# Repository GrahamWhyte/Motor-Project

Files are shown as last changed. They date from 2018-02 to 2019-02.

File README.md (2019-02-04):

# Motor-Project
3rd Year UBC Design project. 

Objective: Design a system of two motors to control a laser to draw various shapes fast enough to look like a complete image. The motors must be hand-built and controlled with a PID controller. 

Files are organized as follows:

1. Elec391_Project_Gen_1 -> Initial PCB
2. Elec391_Project_Gen_2 -> Revised PCB 
3. Elec391_Project_Software -> Arduino Code and GUI 
4. Tests -> Arduino Code to run various tests on Motor. These are flashed onto the Arduino and then run using main.py in Data
5. Data -> Data logger code and output 
6. Matlab and Simulink -> Various models and Matlab scripts
7. Speed Tests -> A series of tests conducted on the custom motors to see how fast they can go! 
8. Encoder -> Mechanical design of test rig 
9. ControlSlideDeck-B10.pdf: Final presentation

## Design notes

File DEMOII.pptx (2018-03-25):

## B10 – “The Rocket Men”

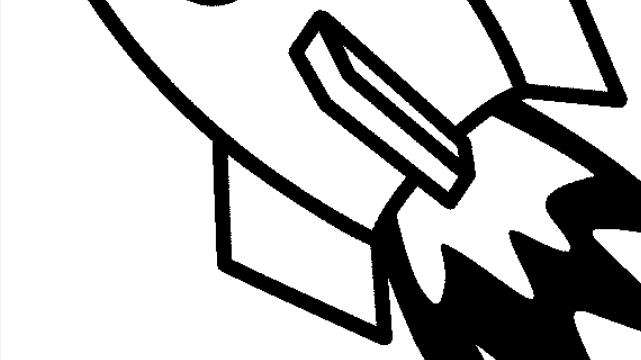
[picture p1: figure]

Control Group
Matthew Gill – 13249157
Graham Whyte - 45688158

## RCGs

Requirement
50 ms Instruction time / Rise Time less than 50 ms
Less than 5% overshoot
2-DOF Spherical Wrist
Simulink Model
Real-Time Controller
Constraints
16 MHz CPU clock speed
Budget ($1000 UBCD + $400 CAD)
Goals
Everything on PCBs
Separate Laser Power – No Dangling Wires from Diode
Animation
Optimal Rise – 25 ms
Satisfied
Satisfied
Satisfied

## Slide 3

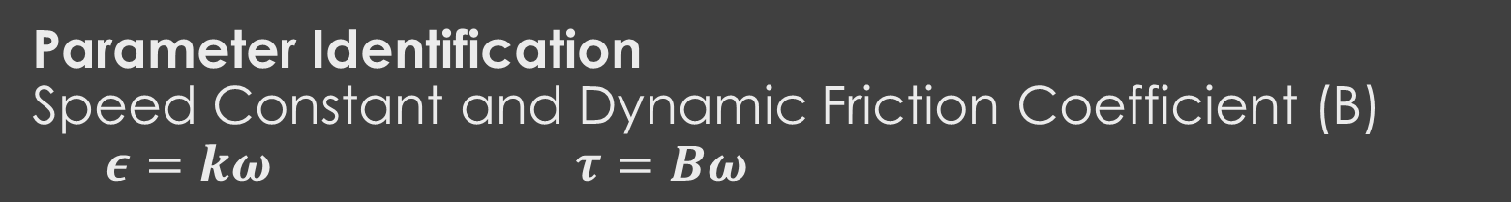
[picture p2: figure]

- Steady State Unloaded Voltage Tests
  - Current Draw (I) and Angular Velocity ( ω ) Recorded
- Back EMF ( ε ) calculated from current & terminal resistance
  - Terminal Resistance & Inductance measured with RLC meter
- Speed Constant (K) as slope of Velocity/Back EMF curve
- Friction Coefficient (B) as Slope of Torque / Speed Curve
  - Torque calculated with: τ=kI

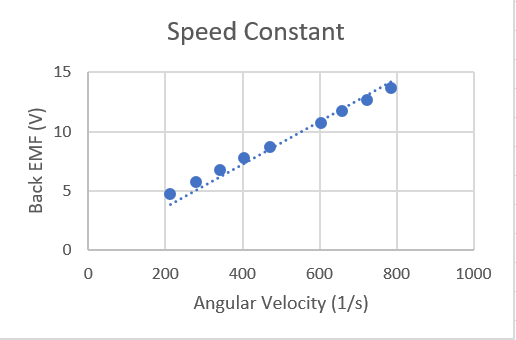
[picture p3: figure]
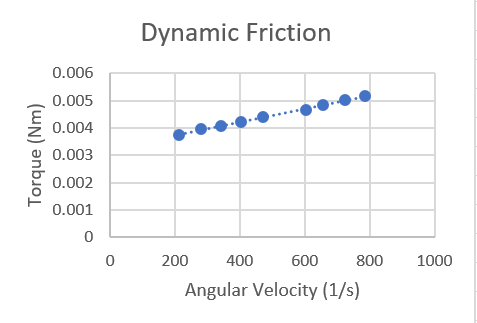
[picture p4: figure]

## Parameter Identification Rotor Inertia (J) - Deceleration test of unloaded motor

J =8.30 gcm^2

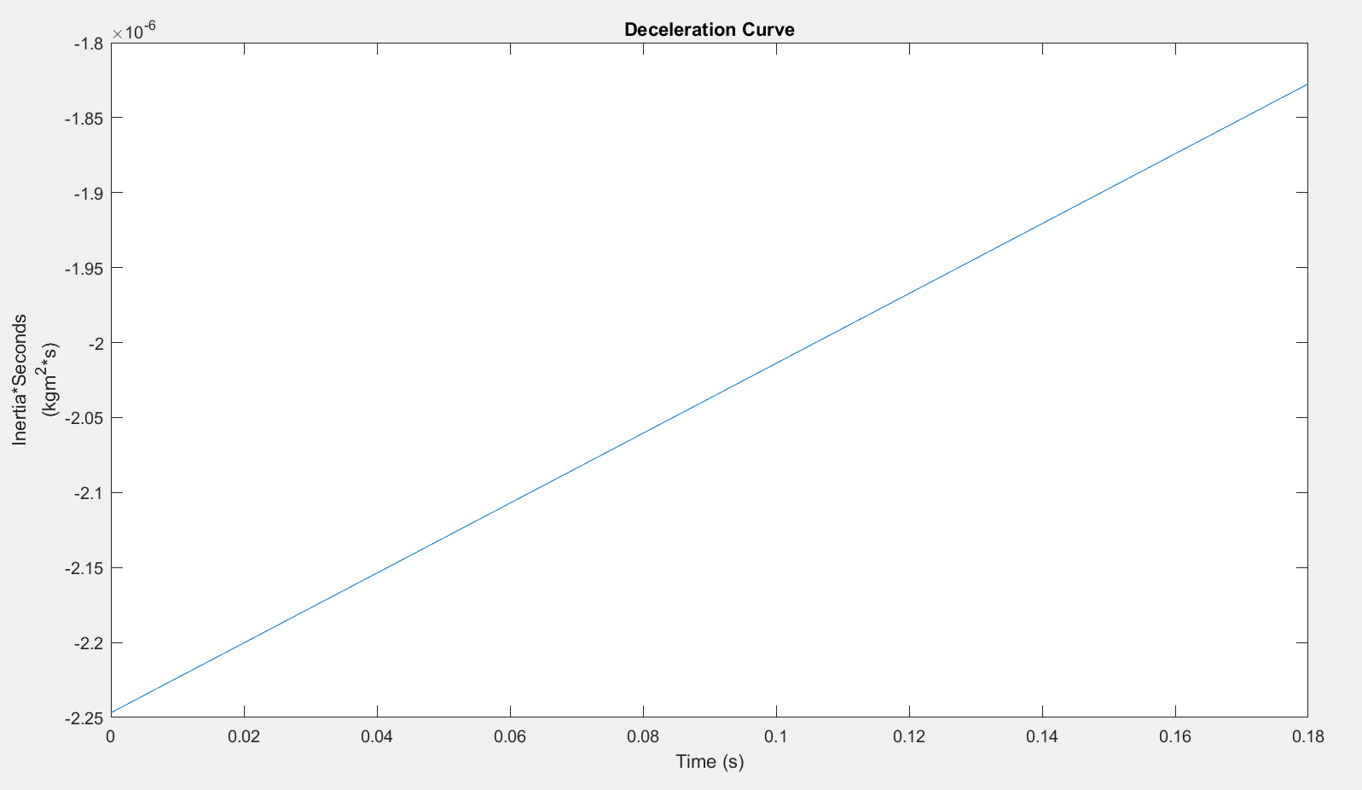
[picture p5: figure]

- Angular System with no external Torque:
0=Jω+Bω
then:
J is Slope of−(B∗ω(t))/(ω(t)) curve
- Power is cut to motor running constant velocity and velocity and acceleration is recorded as motor slows

## Experimental Step Response Curve Fitting

- Step test is conducted by applying a 10V step voltage to motor and recording position of motor
- The Velocity Step Response is obtained by differentiating the Position Step Response
- Utilizing MATLAB's System Identification toolkit a transfer function can then be fitted to the Velocity Response
- Transfer Function from Velocity Step Response
- (ω(s))/(V(s))(2.702x10^4)/(s^2 +38.02s+531)

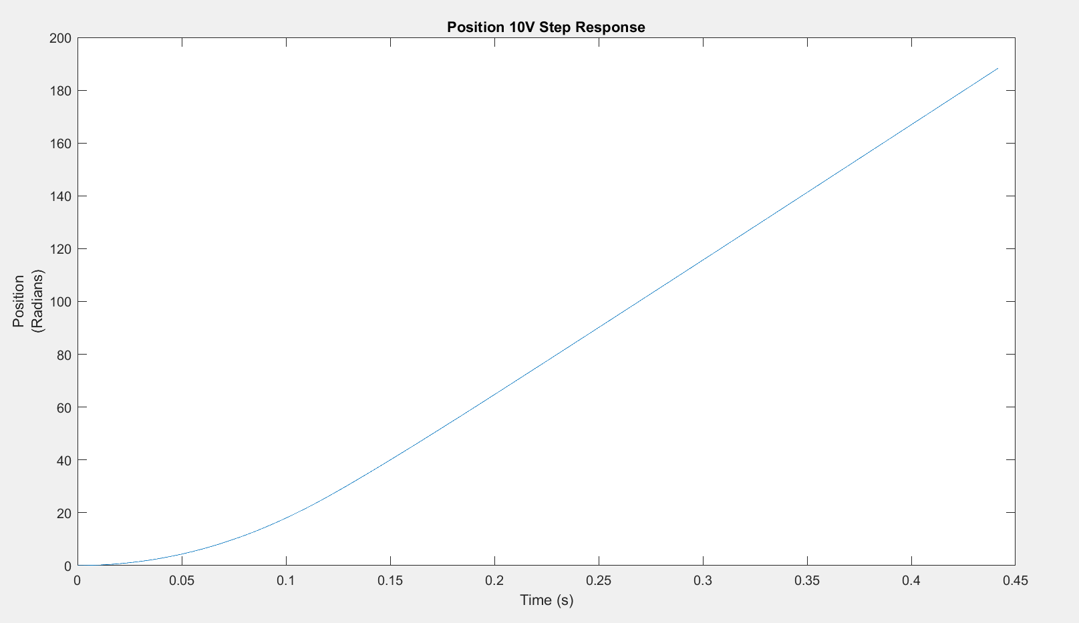
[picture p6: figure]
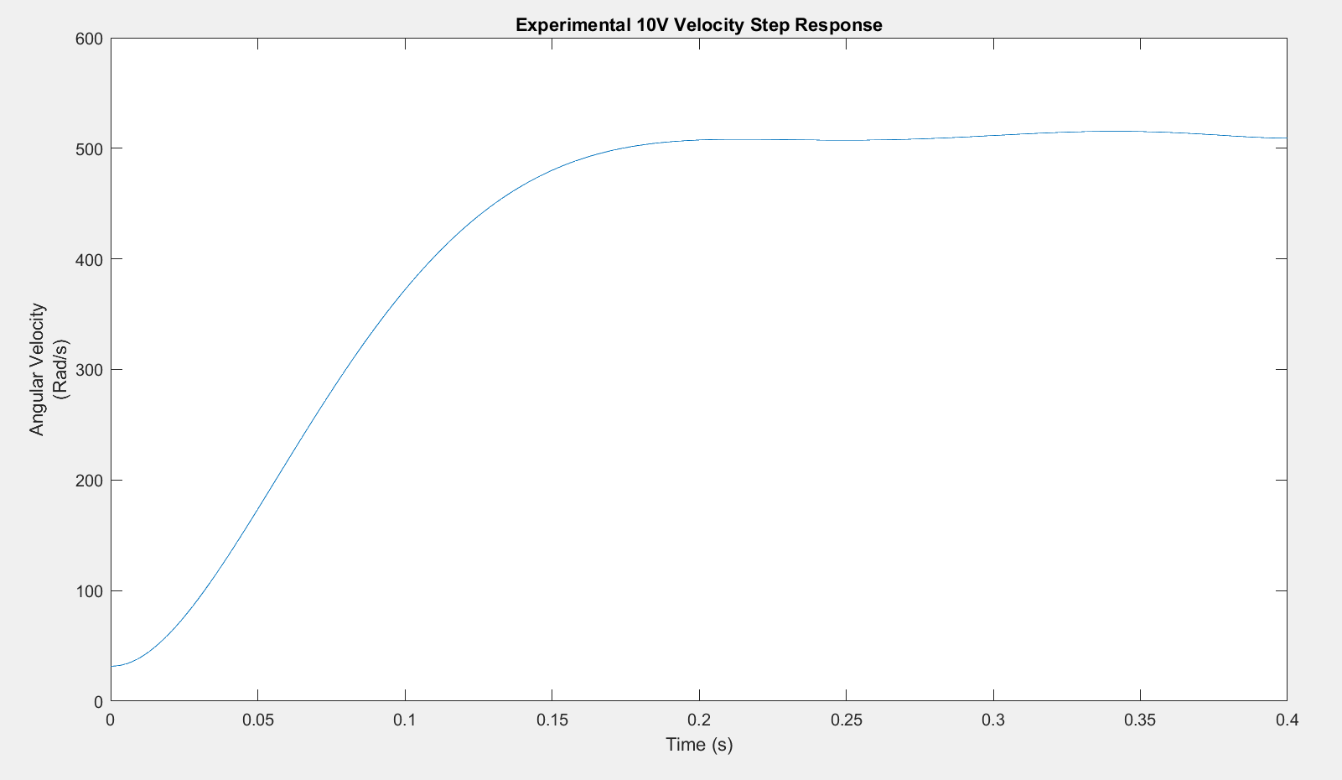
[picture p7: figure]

## Model Verification – Step Response Comparison

- Comparison between Experimental and Modelled Step Responses helps verify model accuracy
- Possible Causes of Difference between Responses:
  - Static Friction is unmodeled
    - Accounts for initial delay of experimental response
  - Current Driver is unmodeled
    - Resistance/Capacitance/Inductance that could effect response

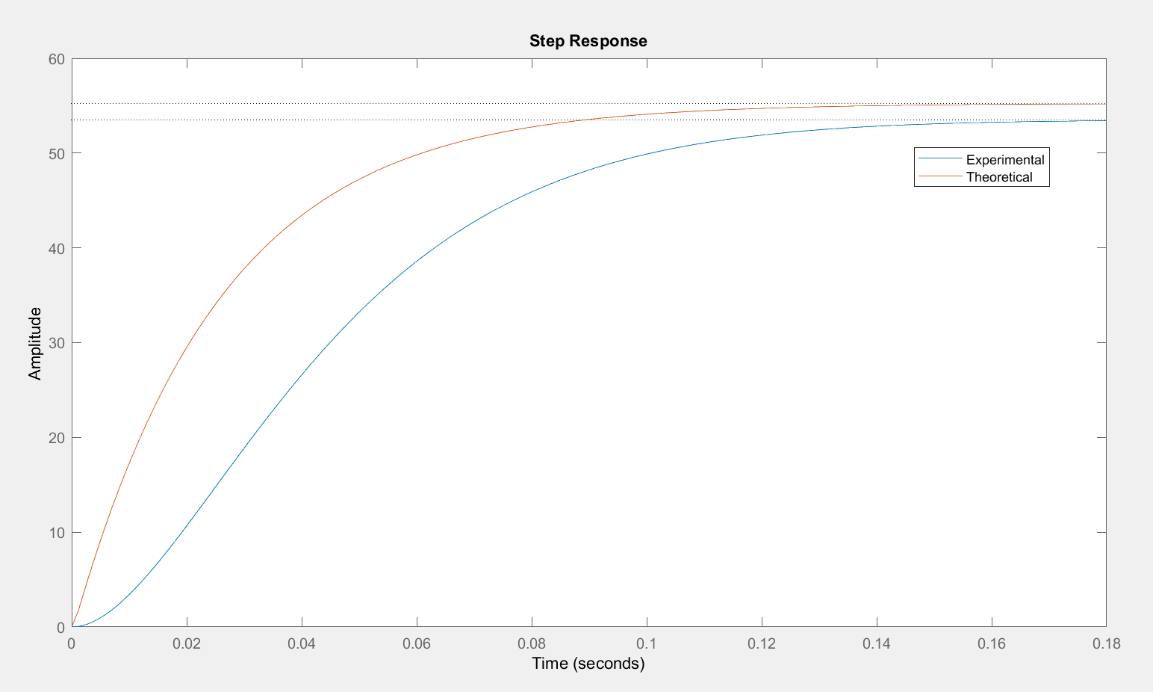
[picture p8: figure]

## Encoder & Slot Detector Attachment

- Fits directly onto face of Jameco Motor.
- Slot Detector friction fitted into slot at tope of attachment
- Advantages:
  - Usable with motor oriented vertically and horizontally
  - Reusable
  - Adjustable

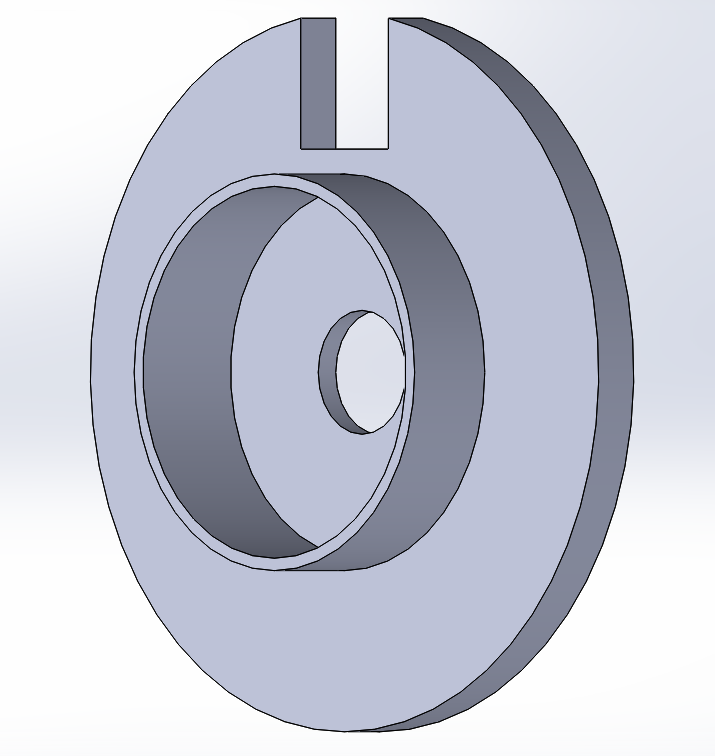
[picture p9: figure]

## Mechanical System Model

- Encoder Disk
  - Modelled as Cylinder rotating about it’s Z-Axis
  - Mass (m) calculated from Encoder Dimensions & density of FR4 (1.850 g/(cm^3) )
    - J_(Encoder) = 1/2∗mr^2 =1/2∗(5.2719)(2.4)^2 =15.18 gcm^2
- Laser Diode Bracket
  - Modelled using SolidWorks Mass Analysis & density of PLA (1.25 g/(cm^3) )
    - J_(Bracket) =0. 177gcm^2
- Laser Diode
  - Modelled as cylinder rotating its y – axis
  - Mass Measured at 2.00 grams
    - J_(Diode) = 1/12m(3r^2 +h^2 )=1/12∗(2.00)(3(0.7)^2 +(2.1)^2 )=0.98 gcm^2

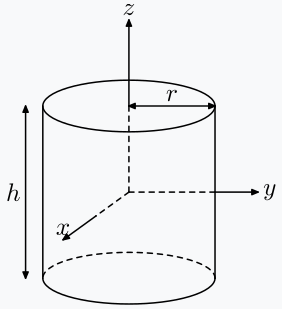
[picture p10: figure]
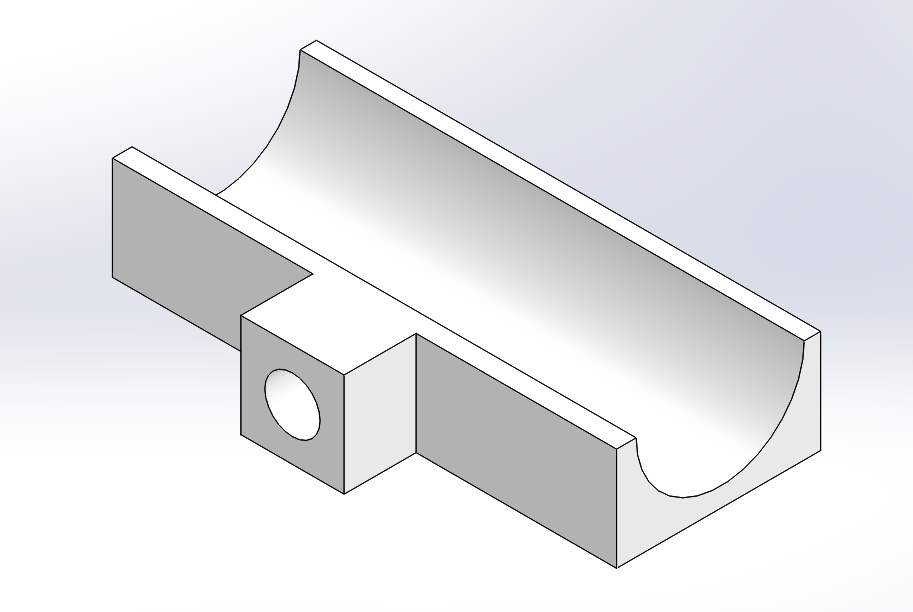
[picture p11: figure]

## Simulink – Block Diagram + Kinematics

- Allows for real time simulation of system
- Builds transfer function blocks from measured parameters
- Parameters in separate MATLAB files to allow for incremental and documented change
- Single Degree of Freedom for Laser Diode with Constant Y_d
(X_d , Y_d ) ⇒ θ_D
Inverse
θ_D =atan(X_D)/(Y_D)
Direct
X_A =tan⁡(θ_A )* Y_A

DC Motor Block

PID Control Block + DC Motor

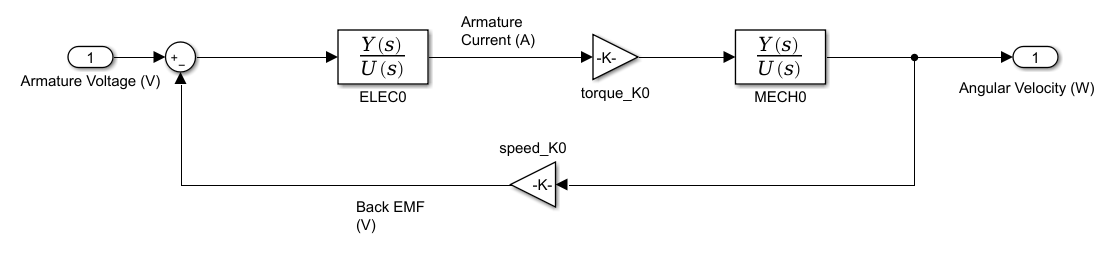
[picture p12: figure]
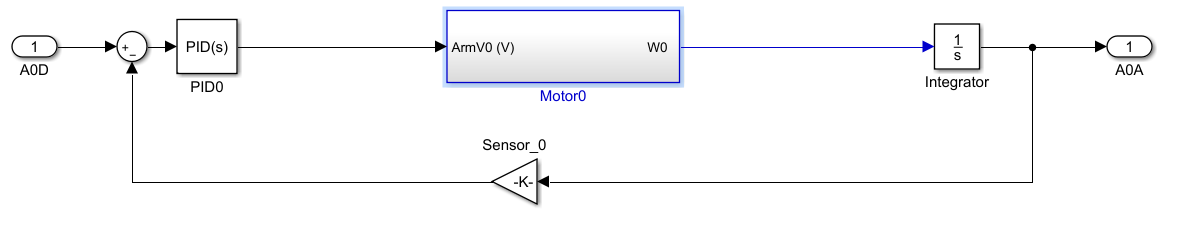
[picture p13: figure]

## PID – PZ Plot & Zero Placement & Root Locus

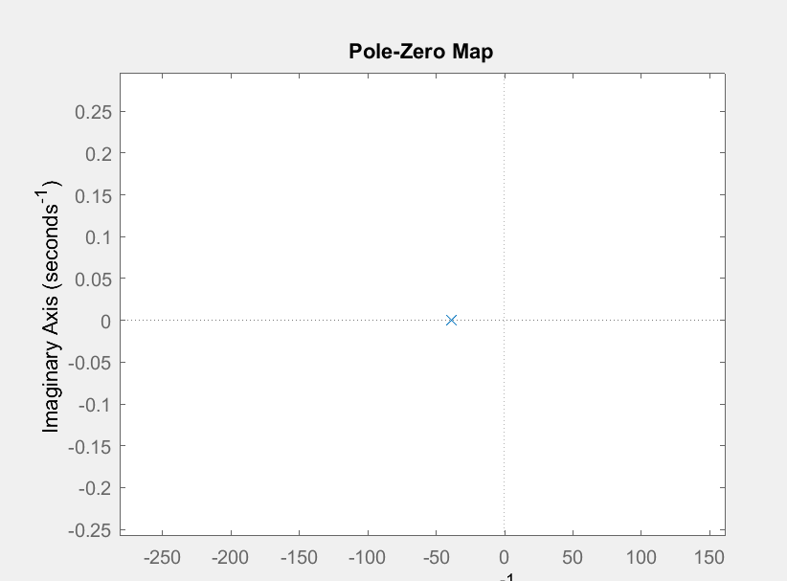
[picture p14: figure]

PZ Plot
  - Additional Pole at S = -3000
    - Assuming contribution is negligible
Starting Zero Placement
  - (s + 5)(s+15)
  - Draw Pole at Zero to left for me stability
  - Draw Pole on the left to right for improved response time
  - No K_U
Starting Gains
K_D = 0.0400
K_P = 0.30
K_I = 0.80

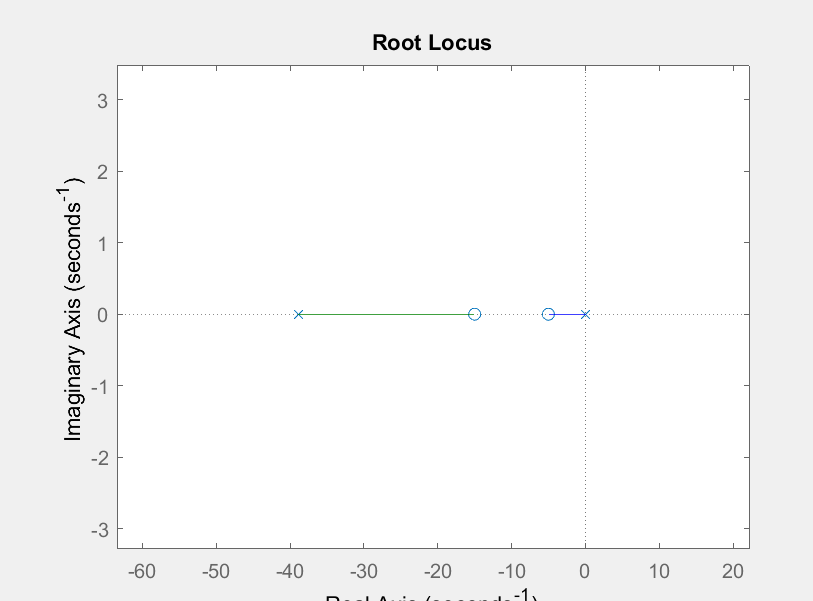
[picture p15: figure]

## Program Block Diagram

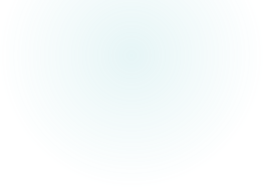
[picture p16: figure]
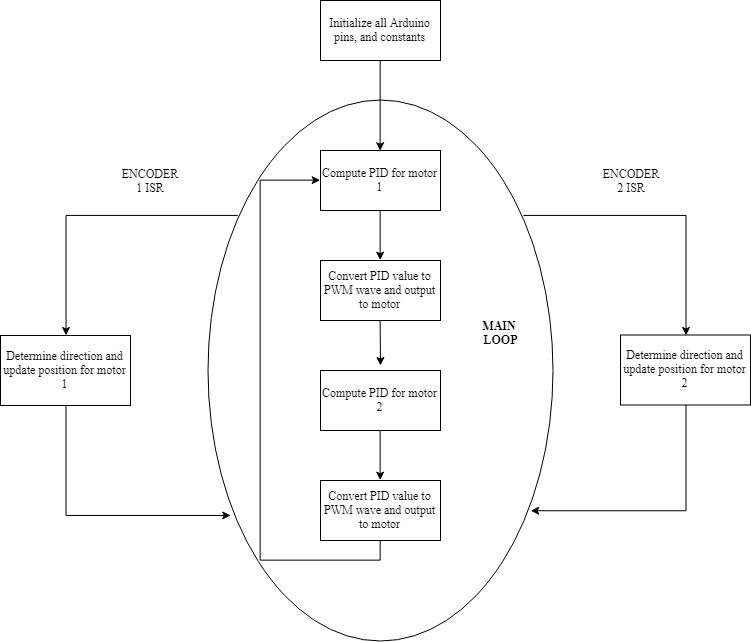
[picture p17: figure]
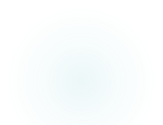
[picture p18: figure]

## PID Pseudocode

1. Record current program time
2. Calculate dt = time – last time
3. Calculate error = desired position – current position
4. Calculate de
  1. IF Setpoint has changed since the last reading, de = -current position – last error
  2. ELSE de = error – last error
5. Calculate total error = total error + error
6. Calculate output = kp*error + ki*total error + kd*de/dt
7. Constrain output between ±255 for Arduino
8. Store time, total error, and desired position for next calculation

## Microcontroller Selection

- Arduino Uno

- Interrupt pins: 2
- PWM pins: 6
- RAM: 2kB
- Readily available and easy to build PCB around

- Arduino Mega

- Interrupt pins:
- PWM pins: 15
- RAM: 8kB
- Need to order in, challenging to build PCB around

## PCB Top Level Design

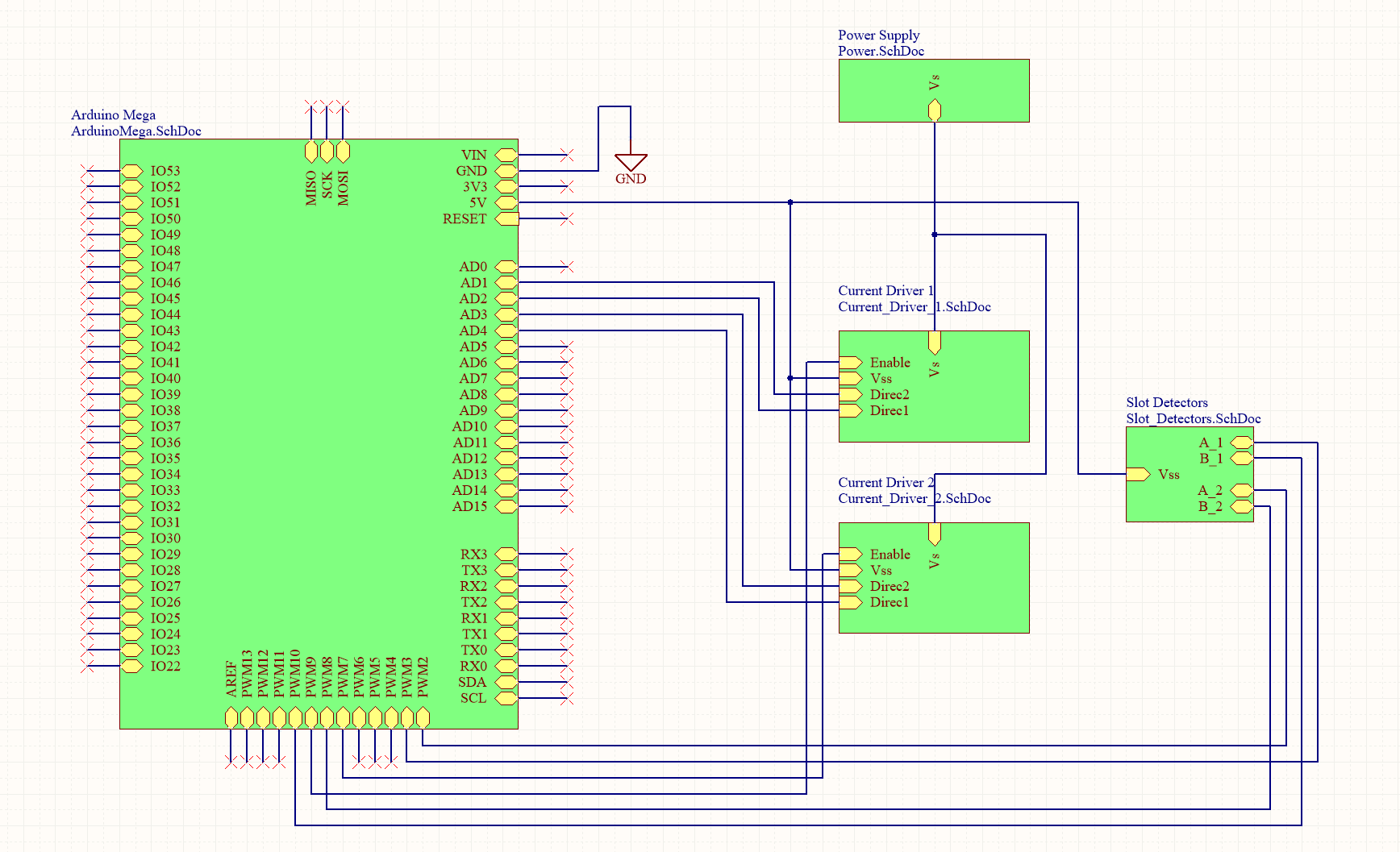
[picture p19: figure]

## PCB Layout

- All ground connections connected to polygon pour

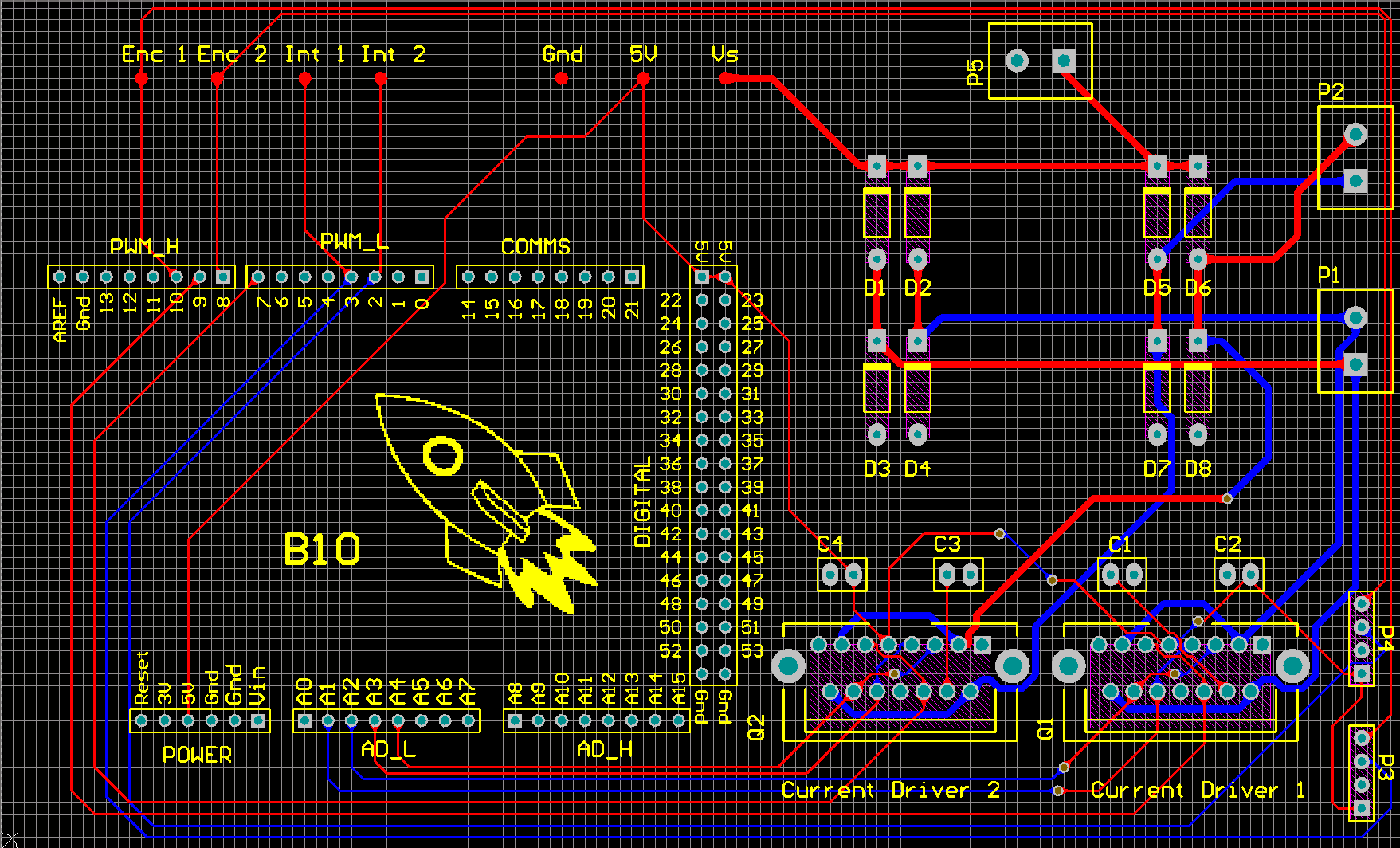
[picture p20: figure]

## PCBA

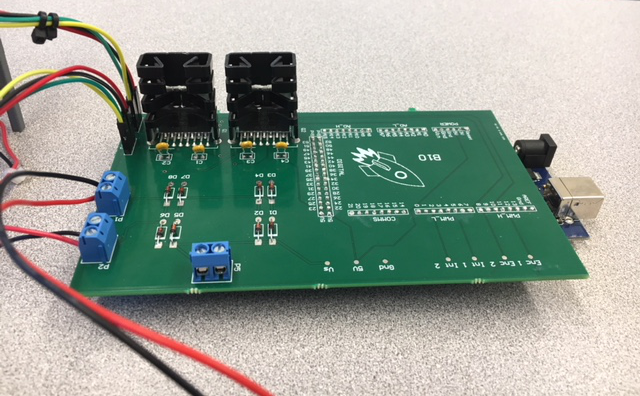
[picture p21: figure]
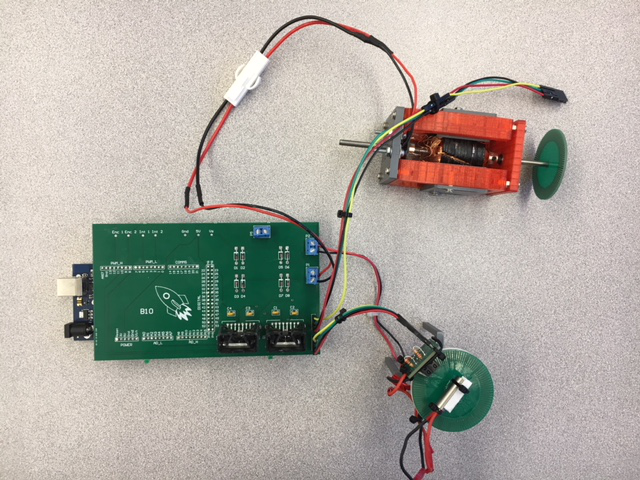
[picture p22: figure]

## Encoder ISR Pseudocode

1. ISR triggers on falling edge of Slot Detector A
2. Check state of Slot Detector B
  1. If Slot Detector B is high, direction is forwards
    1. Increment displacement (number of interrupts from initial position)
  2. If Slot Detector B is low, direction is backwards
    1. Decrement displacement
3. Convert displacement to radians:
Displacement_(rad) =Displacement∗3.6/180

## PCB Future Improvements

- Reduce noise from custom motor
  - Add mechanical cutout between motors
  - Replace ground plane with multiple small ground planes that don’t come near motors
  - Add capacitor across motor terminals
  - Add small inductors in series with motors to prevent large currents in one motor from affecting the other
- Reduce size of PCB
  - Remove Arduino daughter board
- Add additional power ports
  - Banana plugs, barrel connector

## Summary

- Currently Have Operational Real-Time Controlled 1-DOF System
  - Satisfactory Overshoot
- Fully operational Parameter Acquisition Procedure
- Accurate Model of System
- Alpha Version of PCB designed and manufactured

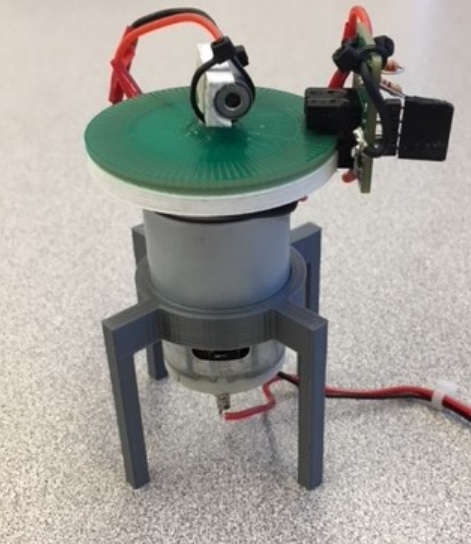
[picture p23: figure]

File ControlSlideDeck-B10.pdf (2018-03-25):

2018-03-09

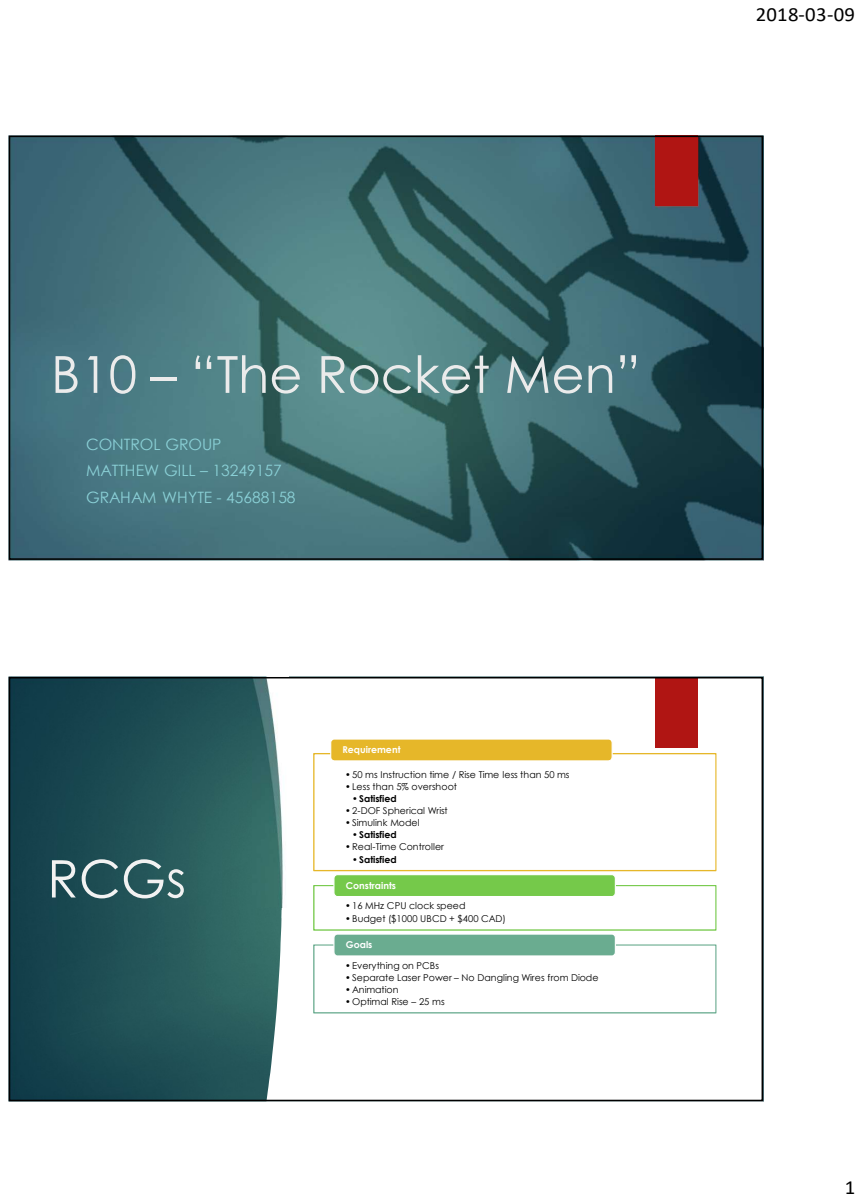
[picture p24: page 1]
CONTROL GROUP MATTHEW GILL – 13249157 GRAHAM WHYTE - 45688158; RCGs; Requirement; Constraints; Goals

B10 – “The Rocket Men”

• 50 ms Instruction time / Rise Time less than 50 ms
• Less than 5% overshoot •Satisfied

• 2-DOF Spherical Wrist
• Simulink Model •Satisfied

• Real-Time Controller •Satisfied

• 16 MHz CPU clock speed
• Budget ($1000 UBCD + $400 CAD)

• Everything on PCBs
• Separate Laser Power – No Dangling Wires from Diode
• Animation
• Optimal Rise – 25 ms

2

Parameter Identification; Steady State Unloaded Voltage Tests; meter; Torque calculated with: τ = kI

## Speed Constant and Dynamic Friction Coefficient (B)

- Current Draw (I) and Angular Velocity (ω) Recorded
- Back EMF (ε) calculated from current & terminal resistance
- Terminal Resistance & Inductance measured with RLC
- Speed Constant (K) as slope of Velocity/Back EMF curve
- Friction Coefficient (B) as Slope of Torque / Speed Curve

Parameter Identification; 0 = Jω̇ + Bω then:; J is Slope of − ∗  ̇ (); curve; velocity and velocity and acceleration is recorded as motor slows; J = 8.30 gcm

### Rotor Inertia (J) - Deceleration test of unloaded motor

- Angular System with no external Torque:
- Power is cut to motor running constant

3

Experimental Step Response Curve Fitting; differentiating the Position Step Response; Velocity Response

- Step test is conducted by applying a 10V step voltage to motor and recording position of motor
- The Velocity Step Response is obtained by
- Utilizing MATLAB's System Identification toolkit a transfer function can then be fitted to the
- Transfer Function from Velocity Step Response

# Model Verification – Step Response Comparison

- Comparison between Experimental and
Modelled Step Responses helps verify model
accuracy
- Possible Causes of Difference between Responses:
- Static Friction is unmodeled
- Accounts for initial delay of experimental response
- Current Driver is unmodeled


- Resistance/Capacitance/Inductance that could effect response

4

Encoder & Slot Detector Attachment; Fits directly onto face of Jameco Motor.; at tope of attachment; Advantages: Usable with motor oriented vertically and horizontally Reusable Adjustable

- Slot Detector friction fitted into slot

Mechanical System Model; Encoder Disk; ∗ 5.2719 2.4  = 15.18 gcm; Laser Diode Bracket; J = 0. 177gcm; Laser Diode; Mass Measured at 2.00 grams; ) = 0.98 gcm

- Modelled as Cylinder rotating about it’s Z-Axis
- Mass (m) calculated from Encoder Dimensions & density of FR4 (1.850
- Modelled using SolidWorks Mass Analysis & density of PLA (1.25
- Modelled as cylinder rotating its y – axis

5

Simulink – Block Diagram + Kinematics; Allows for real time simulation of system Builds transfer function blocks from measured parameters Parameters in separate MATLAB files to allow for incremental and documented change Single Degree of Freedom for Laser Diode with Constant Y; Inverse; θ = atan ; Direct; X = tan (θ)* Y; DC Motor Block; PID Control Block + DC Motor

## PID – PZ Plot & Zero Placement & Root Locus

PZ Plot
- Additional Pole at S = -3000
- Assuming contribution is negligible
Starting Zero Placement
- (s + 5)(s+15)
- Draw Pole at Zero to left for me stability
- Draw Pole on the left to right for improved response time
- No K
Starting Gains
K = 0.0400
K = 0.30
K = 0.80

6

Program Block Diagram
PID Pseudocode

### 1. Record current program time 2. Calculate dt = time – last time 3. Calculate error = desired position – current position 4. Calculate de

1. IF Setpoint has changed since the last reading, de = -current position – last error
2. | ELSE de = error – last error 5. | Calculate total error = total error + error
6. | Calculate output = kp*error + ki*total error + kd*de/dt 7. | Constrain output between ±255 for Arduino

### 8. Store time, total error, and desired position for next

calculation

7

# Microcontroller Selection

## Arduino Uno

- Interrupt pins: 2
- PWM pins: 6
- RAM: 2kB
- Readily available and easy to build PCB around

## Arduino Mega

- Interrupt pins:
- PWM pins: 15
- RAM: 8kB
- Need to order in, challenging to build PCB around

PCB Top Level Design

# PCB Layout


8

- All ground connections
connected to polygon pour

# PCBA

9

Encoder ISR Pseudocode

### 1. ISR triggers on falling edge of Slot Detector

A

### 2. Check state of Slot Detector B

### 1. If Slot Detector B is high, direction is

forwards

### 1. Increment displacement (number of

interrupts from initial position)

### 2. If Slot Detector B is low, direction is

backwards

### 1. Decrement displacement

### 3. Convert displacement to radians:

Displacement = Displacement ∗

3.6
180

PCB Future Improvements; Reduce noise from custom motor; Add mechanical cutout between motors; Add capacitor across motor terminals; affecting the other Reduce size of PCB; Remove Arduino daughter board Add additional power ports; Banana plugs, barrel connector

- Replace ground plane with multiple small ground planes that don’t come near motors
- Add small inductors in series with motors to prevent large currents in one motor from

10

Summary; Currently Have Operational Real-Time Controlled 1-DOF System Satisfactory Overshoot; Fully operational Parameter Acquisition Procedure; Accurate Model of System; Alpha Version of PCB designed and manufactured

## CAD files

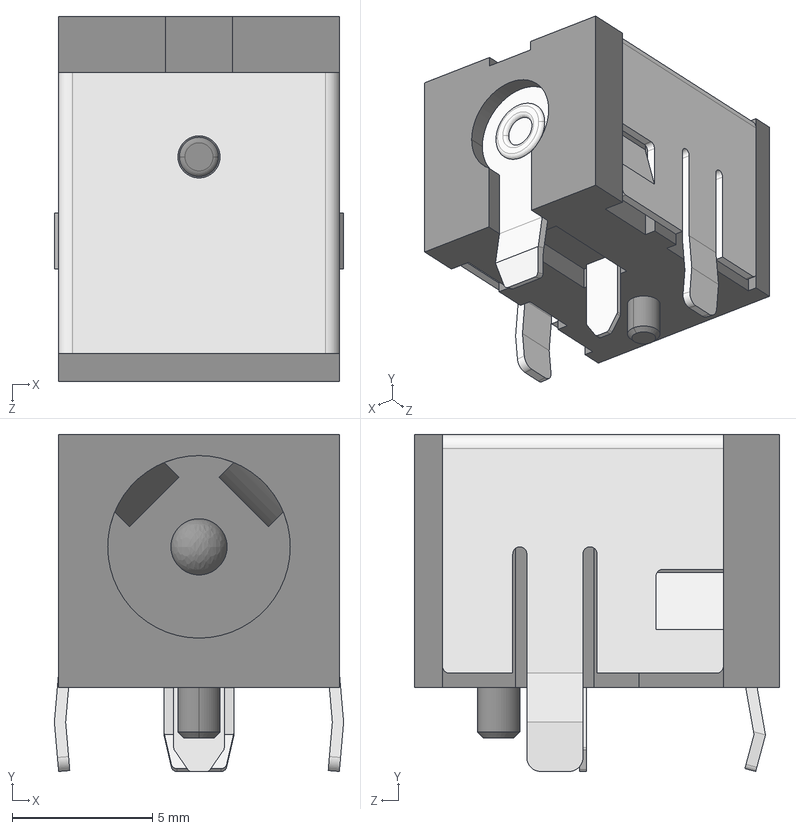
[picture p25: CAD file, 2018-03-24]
Elec391_Project_Gen_2/Models/User Library-PJ-063AH.STEP
10.3 x 12.0 x 13.0 mm
User Library-PJ-063AH_Fillet
User Library-PJ-063AH_PJ_063AH001
User Library-PJ-063AH_PJ_063AH
User Library-PJ-063AH_PJ_063AH002
User Library-PJ-063AH_PJ_063AH003

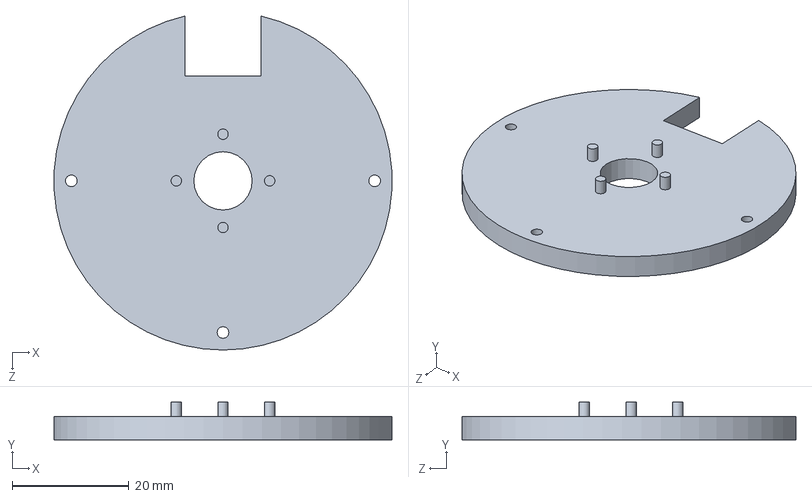
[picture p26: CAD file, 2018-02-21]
encoder/Proto1/diskback.SLDPRT
57.9 x 6.50 x 57.3 mm

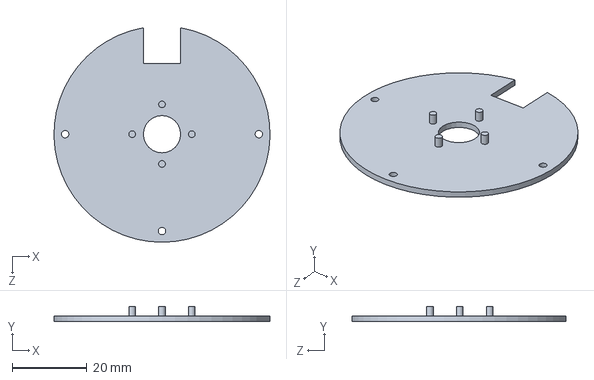
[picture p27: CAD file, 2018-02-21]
encoder/Proto2/diskback2.SLDPRT
58.0 x 4.00 x 57.6 mm

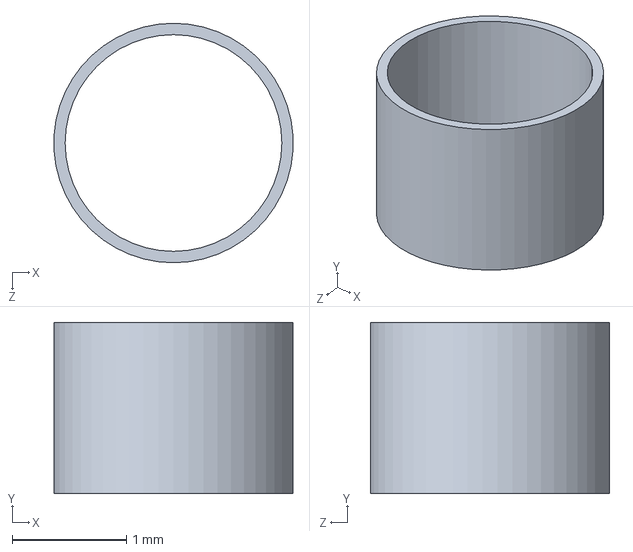
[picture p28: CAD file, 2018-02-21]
encoder/Proto1/rotorstop.SLDPRT
2.10 x 1.50 x 2.10 mm

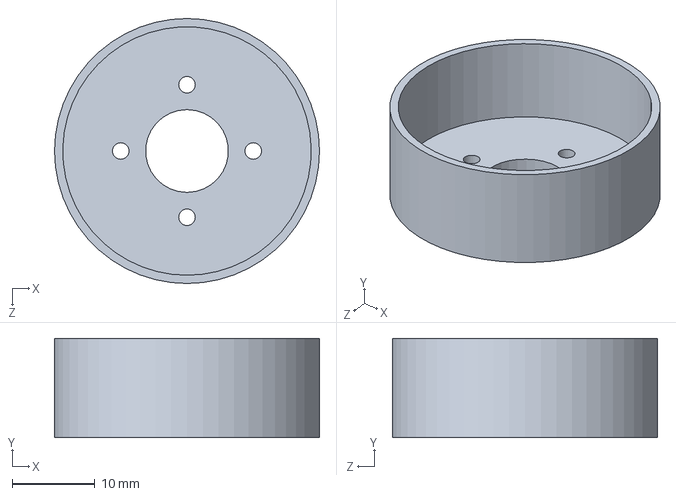
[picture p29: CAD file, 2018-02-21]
encoder/Proto2/motorcap2.SLDPRT
32.0 x 12.0 x 32.0 mm

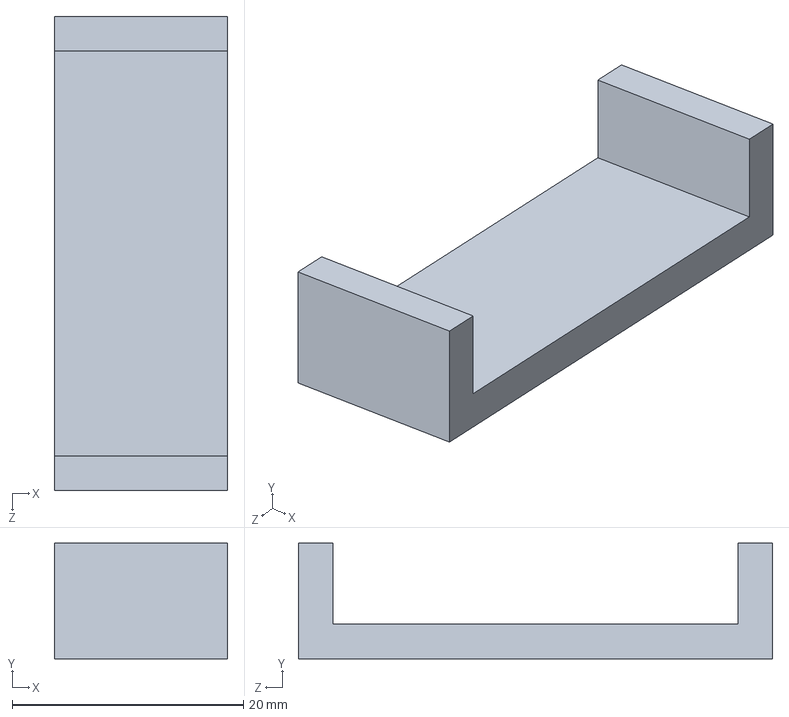
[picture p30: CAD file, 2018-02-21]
encoder/Proto1/clamp.SLDPRT
15.0 x 10.0 x 41.0 mm

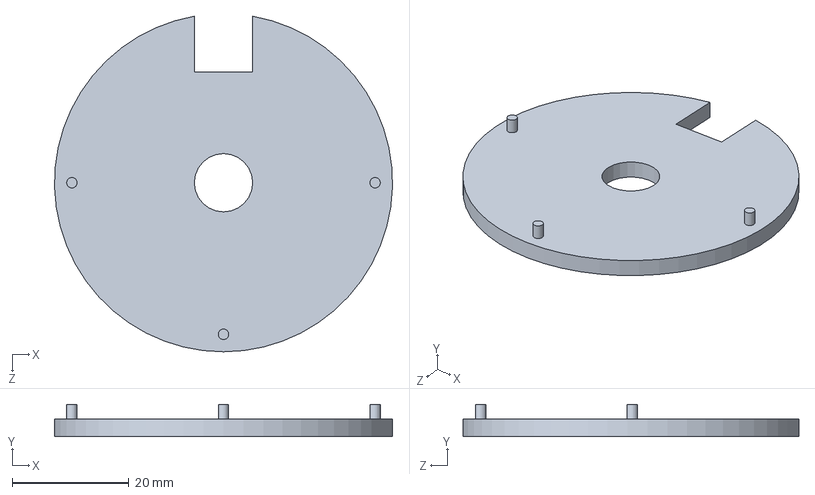
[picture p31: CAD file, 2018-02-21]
encoder/Proto2/diskfront2.SLDPRT
58.0 x 5.50 x 57.6 mm

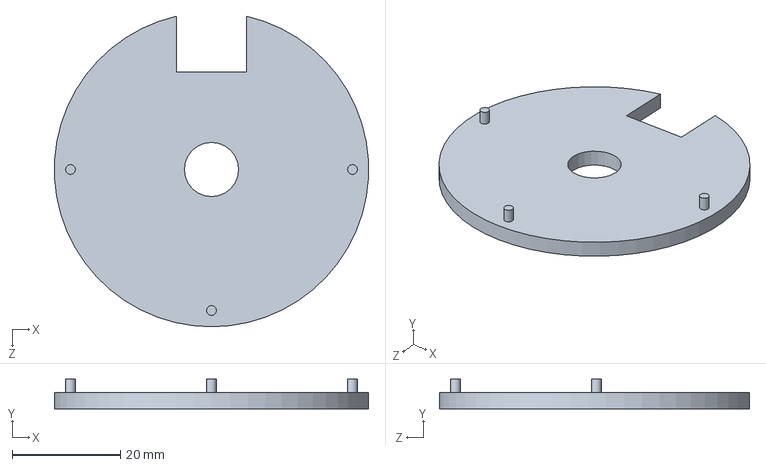
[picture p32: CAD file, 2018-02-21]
encoder/Proto1/diskfront.SLDPRT
57.9 x 5.50 x 57.3 mm

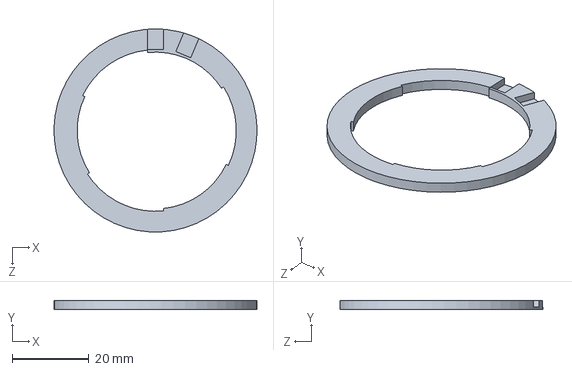
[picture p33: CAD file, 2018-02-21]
encoder/Proto1/face.SLDPRT
52.8 x 2.40 x 52.8 mm

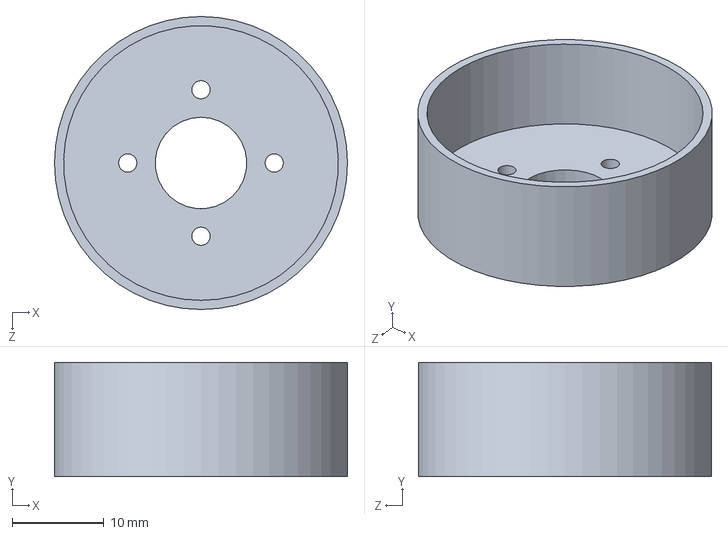
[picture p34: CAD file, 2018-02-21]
encoder/Proto1/motorcap.SLDPRT
32.0 x 12.5 x 32.0 mm

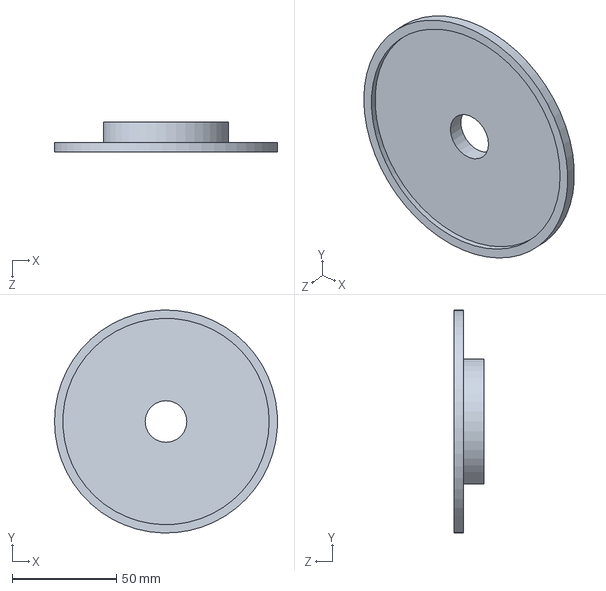
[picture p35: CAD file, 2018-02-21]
encoder/Proto1/base.SLDPRT
107.0 x 107.0 x 14.5 mm

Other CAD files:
encoder/Proto1/base.STL
encoder/Proto1/clamp.STL
encoder/Proto1/diskback.STL
encoder/Proto1/diskfront.STL
encoder/Proto1/face.SLDDRW
encoder/Proto1/motorcap.STL
encoder/Proto1/rotorstop.STL
encoder/Proto2/motorcap2.STL

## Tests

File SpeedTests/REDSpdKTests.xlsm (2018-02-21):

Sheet: Calcs
V | A | IR | Er | Rad/Sec | Torque(Nm)
5 | 0.113 | 0.24069 | 4.75931 | 212.6 | 0.003730695
6 | 0.119 | 0.25347 | 5.74653 | 278.6 | 0.003928785
7 | 0.123 | 0.26199 | 6.73801 | 341.6 | 0.004060845
8 | 0.128 | 0.27264 | 7.72736 | 403.1 | 0.00422592
9 | 0.133 | 0.28329 | 8.71671 | 471.6 | 0.004390995
11 | 0.141 | 0.30033 | 10.69967 | 603.1 | 0.004655115
12 | 0.146 | 0.31098 | 11.68902 | 657 | 0.00482019
13 | 0.152 | 0.32376 | 12.67624 | 722.8 | 0.00501828
14 | 0.156 | 0.33228 | 13.66772 | 785.6 | 0.00515034
 |  | SPEED CONSTANT (Kw)
 |  |  | 0.0155 | Vs
 |  | Dynamic Friction (B)
R |  |  | 2.439e-06 | Nms
2.13
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

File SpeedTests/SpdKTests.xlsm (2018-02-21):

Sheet: Calcs
V | A | IR | Er | Rad/Sec | Torque(Nm)
5 | 0.113 | 0.24069 | 4.75931 | 212.6 | 0.003730695
6 | 0.119 | 0.25347 | 5.74653 | 278.6 | 0.003928785
7 | 0.123 | 0.26199 | 6.73801 | 341.6 | 0.004060845
8 | 0.128 | 0.27264 | 7.72736 | 403.1 | 0.00422592
9 | 0.133 | 0.28329 | 8.71671 | 471.6 | 0.004390995
11 | 0.141 | 0.30033 | 10.69967 | 603.1 | 0.004655115
12 | 0.146 | 0.31098 | 11.68902 | 657 | 0.00482019
13 | 0.152 | 0.32376 | 12.67624 | 722.8 | 0.00501828
14 | 0.156 | 0.33228 | 13.66772 | 785.6 | 0.00515034
 |  | SPEED CONSTANT (Kw)
 |  |  | 0.0155 | Vs
 |  | Dynamic Friction (B)
R |  |  | 2.439e-06 | Nms
2.13
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

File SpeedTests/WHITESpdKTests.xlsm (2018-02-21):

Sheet: Calcs
V | I | IR | Er | Rad/Sec | Torque(Nm)
7 | 0.112 | 0.28896 | 6.71104 | 336.64 | 0.001769279329
9 | 0.12 | 0.3096 | 8.6904 | 459.38 | 0.001895656423
11 | 0.125 | 0.3225 | 10.6775 | 581.8 | 0.001974642108
13 | 0.133 | 0.34314 | 12.65686 | 716.21 | 0.002101019203
15 | 0.141 | 0.36378 | 14.63622 | 831.6 | 0.002227396298
18 | 0.166 | 0.42828 | 17.57172 | 1024.2 | 0.002622324719
 |  | SPEED CONSTANT (Kw)
 |  |  | 0.01579713686 | Vs
 |  | Dynamic Friction (B)
R |  |  | 2.968829614e-06 | Nms
2.58

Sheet: 7V
RawTime | Scaled(uS) | Scaled(s) | rawDisp | Disp(rad) | V (rad/Sec)
33948 | 0 | 0 | 0 | 0 |  | Rad/Sec | RPM
33968 | 20 | 2e-05 | 1 | 0.06283185307 | 3141.592654 | 335.6419555 | 3205.144579
34156 | 208 | 0.000208 | 2 | 0.1256637061 | 334.2119844
34348 | 400 | 0.0004 | 3 | 0.1884955592 | 327.2492347
34536 | 588 | 0.000588 | 4 | 0.2513274123 | 334.2119844
34724 | 776 | 0.000776 | 5 | 0.3141592654 | 334.2119844
34916 | 968 | 0.000968 | 6 | 0.3769911184 | 327.2492347
35108 | 1160 | 0.00116 | 7 | 0.4398229715 | 327.2492347
35296 | 1348 | 0.001348 | 8 | 0.5026548246 | 334.2119844
35484 | 1536 | 0.001536 | 9 | 0.5654866776 | 334.2119844
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

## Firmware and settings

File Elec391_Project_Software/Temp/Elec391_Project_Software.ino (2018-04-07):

#include <TimerOne.h>
#include <TimerThree.h>
#include <avr/pgmspace.h>

#define LASER_DIREC_2   A1
#define LASER_DIREC_1   A2
#define MIRROR_DIREC_2  A3
#define MIRROR_DIREC_1  A4

#define LASERSETSIZE 31
#define MIRRORSETSIZE 12

#define INTERRUPT_TO_DEG  0.9
#define SUPPLY_VOLTAGE    14
#define ANGLE_MAX         1.047197        // Approx. 60 degrees 
#define ANGLE_MIN         -1.047197       // Approx. -60 degrees 

//#define FILTER_COEF         4099
#define FILTER_COEF         4007
#define SETPOINT_ARRAY_SIZE 101
#define TERMINATION_VAL -1000

//Kp Laser Correction
#define  LASER_MOD 0.375

bool laser_direction;

union {
  float floatVal; 
  byte floatBuf[4]; 
} floatData; 

union {
  int intVal; 
  byte intBuf[2]; 
} intData; 

//const int LASER_ARRAY_SIZE = 27; 
//const int MIRROR_ARRAY_SIZE = 1; 

// Set control frequency 
int controlTime_us = 1000;                  // PID update time in us 
double controlTime_s = controlTime_us/1E6;  // PID update time in s

// Index to keep track of how far through the setpoint array we are 
int setpointIndex = 0; 
bool setpointDir= true; 


// Timer 1 flag
bool t1Flag = false; 

// Arrays of setpoints for each shape. Will be overwritten every time the shape changes 
volatile double setpointArray_laser [SETPOINT_ARRAY_SIZE]; 
volatile double setpointArray_mirror [SETPOINT_ARRAY_SIZE]; 

// Character to recieve from Serial. Will determine which shape to draw
char shapeSignal = ""; 
char circleSignal = 'c'; 
char triangleSignal = 'l'; 
char squareSignal = 's'; 
char lineSignal = 'l'; 

// Setpoint Arrays
const double setpoint_laser_line [SETPOINT_ARRAY_SIZE] PROGMEM = {25.2, 21.6, 18, 14.4, 
                                                               10.8, 7.2, 3.6, 0, -3.6, -7.2, -10.8, -14.4, -18, -21.6,
                                                               -25.2, TERMINATION_VAL}; 
const double setpoint_mirror_line [SETPOINT_ARRAY_SIZE] PROGMEM = {61.2, 61.2, 61.2, 61.2,
                                                                  61.2, 61.2, 61.2, 61.2, 61.2, 61.2, 61.2, 61.2, 61.2, 61.2,
                                                                  61.2, TERMINATION_VAL};
                                                                  
const double setpoint_laser_circle [SETPOINT_ARRAY_SIZE] PROGMEM = {18,14.4,10.8,7.2,3.6,7.2,10.8,14.4, TERMINATION_VAL}; 
const double setpoint_mirror_circle [SETPOINT_ARRAY_SIZE] PROGMEM = {43.2,46.8,50.4,46.8,43.2,39.6,36,39.6, TERMINATION_VAL};

const double setpoint_laser_square [SETPOINT_ARRAY_SIZE] PROGMEM = {  0,
                                                                    18,18,18,
                                                                       0,
                                                                    -18,-18,-18,
                                                                   TERMINATION_VAL}; 
const double setpoint_mirror_square [SETPOINT_ARRAY_SIZE] PROGMEM = {43.2,
                                                                     43.2,52.4,57.6,
                                                                     57.6,
                                                                     57.6, 52.4,43.2,
                                                                      TERMINATION_VAL};

const double setpoint_laser_triangle [SETPOINT_ARRAY_SIZE] PROGMEM = {0,3.6,7.2,10.8,7.2,3.6,0,-3.6,-7.2,-10.8,-7.2,-3.6,TERMINATION_VAL}; 
const double setpoint_mirror_triangle [SETPOINT_ARRAY_SIZE] PROGMEM = {43.2,43.2,43.2,43.2,46.8,50.4,54,50.4,46.8,43.2,43.2,43.2,TERMINATION_VAL};                                                                                                                     
const double setpoint_laser_zero [SETPOINT_ARRAY_SIZE] PROGMEM = {0, TERMINATION_VAL}; 
const double setpoint_mirror_zero [SETPOINT_ARRAY_SIZE] PROGMEM = {0, TERMINATION_VAL}; 

const double setpoint_laser_list[LASERSETSIZE] = {-54,-50.4,-46.8,-43.2,-39.6,-36,-32.4,-28.8,-25.2,-21.6,-18,-14.4,-10.8,-7.2,-3.6,0,3.6,7.2,10.8,14.4,18,21.6,25.2,28.8,32.4,36,39.6,43.2,46.8,50.4,54};
const double setpoint_mirror_list[MIRRORSETSIZE] = {28.8,32.4,36,39.6,43.2,46.8,50.4,54,57.6,61.2,64.8,68.4};
/*************************
        Laser motor
**************************/

// Digital Pins
int motorPin_laser = 9;
int encoderPin_laser = 3;
int encoderPin2_laser = 18;

int homingPin_laser = 20; 

// Initial displacement
int displacement_laser = 0;

// PID values
double errorTotal_laser = 0; 
double lastError_laser = 0; 
double lastSetpoint_laser = 0; 
double lastTime_laser = 0; 

double input_laser = 0, output_laser = 0, setpoint_laser = 0;


double kp_laser = 0.8618;
double ki_laser = 1.0035;
double kd_laser = 0.19066;


/*************************
        Mirror motor
**************************/

// Digital Pins
int motorPin_mirror = 7;
int encoderPin_mirror = 2;
//int encoderPin2_mirror = 8;
int encoderPin2_mirror = 19;        // Will change on new PCB

int homingPin_mirror = 21; 

// Initial displacement
int displacement_mirror = 0;

// PID values
double errorTotal_mirror = 0, lastError_mirror = 0, lastSetpoint_mirror = 0, lastTime_mirror = 0; 

double input_mirror = 0, output_mirror = 0, setpoint_mirror= 0;


double kp_mirror = 1.2;
double ki_mirror = 0.120;
double kd_mirror = 0.161;

void setup() {

 // Open serial port
  Serial.begin(9600);
  
  // Configure pins for Laser motor
  pinMode(motorPin_laser, OUTPUT);
  pinMode(encoderPin_laser, INPUT);
  pinMode(encoderPin2_laser, INPUT);
  pinMode(LASER_DIREC_1, OUTPUT);
  pinMode(LASER_DIREC_2, OUTPUT);
  pinMode(homingPin_laser, INPUT); 

  // Configure ISR for mirror motor encoder slots
  attachInterrupt(digitalPinToInterrupt(encoderPin_laser), laser_encoder_ISR_1, CHANGE);
  attachInterrupt(digitalPinToInterrupt(encoderPin2_laser), laser_encoder_ISR_2, CHANGE);
  
  // Configure pins for Mirror motor
  pinMode(motorPin_mirror, OUTPUT);
  pinMode(encoderPin_mirror, INPUT);
  pinMode(encoderPin2_mirror, INPUT);
  pinMode(MIRROR_DIREC_1, OUTPUT);
  pinMode(MIRROR_DIREC_2, OUTPUT);
  pinMode(homingPin_mirror, INPUT); 

//
//  Serial.println("Homing Begin"); 
//  homing(); 
//  Serial.println("Homing Done"); 
//  

  // Configure ISR for mirror motor encoder slots
  attachInterrupt(digitalPinToInterrupt(encoderPin_mirror), mirror_encoder_ISR_1, CHANGE);
  attachInterrupt(digitalPinToInterrupt(encoderPin2_mirror), mirror_encoder_ISR_2, CHANGE);
  
  // Configure Timer 1. PID values will be updated every time this timer interrupts
  Timer1.initialize(controlTime_us);             // Interrupt time in us
  Timer1.attachInterrupt(timer_one_ISR);

  // Configure Timer 3. The setpoint for both motors will update every time this timer interrupts
  Timer3.initialize(convert_to_micro_seconds(0.05));             // Enter time in seconds, will be converted 
  Timer3.attachInterrupt(update_setpoint);


  /*
   * Uncomment this function if we're not sure if the circuit is working. Make sure it is commented out 
   * before actually running the program
  */
//   testMotor(); 
//  
  // Homing


  
  // Initially draw a square
  populate_setpoint_arrays(setpoint_laser_line, setpoint_mirror_line); 
//  readShape('t'); 

  // Wait 500ms for shit to get not fucked
  delay(500); 

}



bool commandFlag = false; 
bool lenFlag = false; 
bool dataFlag = false; 

int dataIndex = 0; 
int command; 
int len; 
byte *data; 
byte *buff;

double *laser_array; 
double *mirror_array; 

  
//char recievedChar = 'g'; 
void loop() {
  // Make sure at least 3 bytes are available
  if (Serial.available()>0) {
    readShape(); 
  }

//   if (Serial.available()) {
//      Serial.readBytes(buff, 1); 
//      if (!commandFlag) {
//        command = (int)buff[0];
//        commandFlag = true;
//      } else if (!lenFlag) {
//        len = (int)buff[0];
//        lenFlag = true;
//      } else if (!dataFlag) {
//        data[dataIndex] = (byte)buff[0];
//        dataIndex++;
//        if (dataIndex >= len) {
//          dataFlag = true;
////          Serial.write((byte)command);
////          Serial.write((byte)len);
////          for (int i = 0; i < len; i++) {
////            Serial.write(data[i]);
////          }
//        }
//      } else {
//        commandFlag = false;
//        lenFlag = false;
//        dataFlag = false;
//        
//        if (command == 0) {  
//      
//        switch (data[0]) {
//        
//          case 'c': 
//            laser_array = setpoint_laser_circle; 
//            mirror_array = setpoint_mirror_circle; 
//            break; 
//      
//          case 's':
//            laser_array = setpoint_laser_square; 
//            mirror_array = setpoint_mirror_square; 
//            break; 
//      
//          case 't':
//            laser_array = setpoint_laser_triangle; 
//            mirror_array = setpoint_mirror_triangle; 
//            break; 
//      
//          case 'l':
//            laser_array = setpoint_laser_line; 
//            mirror_array = setpoint_mirror_line; 
//            break;
//    
//        // Make sure nothing weird happens if an unexpected signal comes through
//        default: 
//          laser_array = setpoint_laser_line; 
//          mirror_array = setpoint_mirror_line; 
//          break; 
//    
//      }
//      populate_setpoint_arrays(laser_array, mirror_array); 
//  }
//        
//        dataIndex = 0;
//      }
//   }
  
  /*
   * Debugging serial prints 
   * Probably won't work when GUI is implemented
//   */
//  Serial.print(input_laser);
//  Serial.print(","); 
//  Serial.println(setpoint_laser);  
//  Serial.print(input_mirror);
//  Serial.print(", "); 
//  Serial.println(setpoint_mirror);
//  Serial.println(lastTime_laser); 
//

  
//  Serial.println(setpoint_mirror); 


  if (t1Flag) 
    update_pid(); 
}

long convert_to_micro_seconds (double value) {
  long output = round(value*1E6); 
  return output; 
}

void homing() {

  // Rotate until slot detector hits gap
  while(digitalRead(homingPin_mirror)) {
    analogWrite(motorPin_mirror, 100);   
    analogWrite(MIRROR_DIREC_2, 255);
    analogWrite(MIRROR_DIREC_1, 0); 
  }
  analogWrite(motorPin_mirror, 0);
  displacement_mirror = 0; 

  while(digitalRead(homingPin_laser)) {
    analogWrite(motorPin_laser, 100);   
    analogWrite(LASER_DIREC_2, 255);
    analogWrite(LASER_DIREC_1, 0); 
  }
  
  displacement_laser = 0;
//  analogWrite(motorPin_laser, 0);
//  Serial.println("Laser Motor Done"); 

}

void populate_setpoint_arrays (double *laser_shape, double *mirror_shape) {

  for (int i = 0; i < SETPOINT_ARRAY_SIZE; i++) {
    setpointArray_laser[i] = pgm_read_float(&laser_shape[i]);
    setpointArray_mirror[i] = pgm_read_float(&mirror_shape[i]);

//    if (setpointArray_laser[i] != TERMINATION_VAL){
//      Serial.write('m'); 
//      sendFloat(setpointArray_mirror[i]);  
//      Serial.write('l');
//      sendFloat(setpointArray_laser[i]);
//    }
  }  
}


void readShape() {
  double *laser_array;
  double *mirror_array;  

  int *arrayOfFun; 
  char option = 'q'; 

  byte *test; 

  static bool commandFlag = false; 
  static bool lenFlag = false; 
  static bool dataFlag = false; 

  static int dataIndex = 0; 
  static int command; 
  static int len; 
  static int data; 

  long newSpeed = 0; 

  Serial.readBytes(test, 1); 
//  Serial.write(test[0]);

  if (!commandFlag) {
    command = test[0]; 
    commandFlag = true;
  }
  else if (!lenFlag) {
    len = test[0];  
    lenFlag = true; 
  }
  else if (!dataFlag) {
    data = test[0]; 
    dataFlag = true;
//    if (dataIndex < len) {
//      data[dataIndex] = test[0];
//      dataIndex++; 
//    }
//    else {
//      dataFlag = true; 
//    }
  }

  if (dataFlag){
    
    if (command == 0) {  
      
        switch (data) {
        
          case 'c': 
            laser_array = setpoint_laser_circle; 
            mirror_array = setpoint_mirror_circle; 
            break; 
      
          case 's':
            laser_array = setpoint_laser_square; 
            mirror_array = setpoint_mirror_square; 
            break; 
      
          case 't':
            laser_array = setpoint_laser_triangle; 
            mirror_array = setpoint_mirror_triangle; 
            break; 
      
          case 'l':
            laser_array = setpoint_laser_line; 
            mirror_array = setpoint_mirror_line; 
            break;
    
        // Make sure nothing weird happens if an unexpected signal comes through
        default: 
          laser_array = setpoint_laser_line; 
          mirror_array = setpoint_mirror_line; 
          break; 
    
      }
      populate_setpoint_arrays(laser_array, mirror_array); 
  }

  /* Command = 1: Change update speed
   * Convert 4 byte array into float and update timer
   */
//  if (command == 1){
//
//    for (int i = 0; i<4; i++){
//      newSpeed = (newSpeed<<8)|data[i]; 
//    }
//    
//    Timer3.setPeriod(convert_to_micro_seconds((newSpeed/100))); 
//  }
//
//  if (command == 2){
//    Serial.println("New XData"); 
//    for (int i = 0; i < 4*len; i++) {
//       
//    }
//  }

  // Reset Flags
  commandFlag = false; 
  lenFlag = false; 
  dataFlag = false; 
  dataIndex = 0; 
  command = 0; 
  len = 0; 
  data = 0;
//  for (int i = 0; i<4; i++){
//    data[i] = 0; 
//  }
 }

}


// Test to make sure current driver circuit is working
// Should not be called during normal operation
void testMotor () {
  while (true) {
    analogWrite(motorPin_laser, 150);   
    analogWrite(LASER_DIREC_2, 255);
    analogWrite(LASER_DIREC_1, 0); 
    analogWrite(motorPin_mirror, 75); 
    analogWrite(MIRROR_DIREC_2, 255);
    analogWrite(MIRROR_DIREC_1, 0); 
  }
}

void sendFloat(double val) {
  byte *bytes = (byte *)&val; 
  Serial.write(bytes, sizeof(val));
}

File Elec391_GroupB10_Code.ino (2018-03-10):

#include <TimerOne.h>

// Direction Pins
#define WhiteDirecPin   A1
#define WhiteDirecPin2  A2
#define RedDirecPin     A3
#define RedDirecPin2    A4

// Assorted Constants
#define INTERRUPT_TO_RAD 0.0628
#define SUPPLY_VOLTAGE 8
#define ANGLE_MAX 0.6
#define ANGLE_MIN -0.6

/*************************
        White motor
**************************/

// Digital Pins
int white_motorPin = 9;
int white_encoderPin = 3;
int white_encoderPin2 = 10;

// Initial displacement
int white_displacement = 0;

// PID values
double white_errorTotal = 0; 
double white_lastError = 0; 
int white_lastTime = 0; 
double white_lastSetpoint = 0; 

double input_white = 0, output_white = 0, setpoint_white = 0;

double kp_white = 1.4;
double ki_white = 0.0005; 
double kd_white = 0.00001; 

/*************************
        Red motor
**************************/

// Digital Pins
int red_motorPin = 7;
int red_encoderPin = 2;
int red_encoderPin2 = 8;

// Initial displacement
int red_displacement = 0;

// PID values
double red_errorTotal = 0; 
double red_lastError = 0; 
int red_lastTime = 0; 
double red_lastSetpoint = 0; 

double input_red= 0, output_red = 0, setpoint_red= 0;

double kp_red = 0.5;
double ki_red = 0; 
double kd_red = 0; 


/*************************
* Setup
* 
* Initializes Timer1, Configures all pins, Attaches interrupts to encoder pins, initializes setpoints
* 
**************************/
void setup() {

  Serial.begin(9600);

  // Configure Timer 1
  Timer1.initialize(100000);             // Interrupt time in us
  Timer1.attachInterrupt(timer_one_ISR);

  // FOR TESTING: initial setpoint
  setpoint_white = ANGLE_MAX;
  setpoint_red = ANGLE_MAX; 

  /*************************
          White motor
  **************************/
  // Configure digital pins

  pinMode(white_motorPin, OUTPUT);
  pinMode(white_encoderPin, INPUT);
  pinMode(white_encoderPin2, INPUT);
  pinMode(WhiteDirecPin, OUTPUT);
  pinMode(WhiteDirecPin, OUTPUT);

  // Configure ISR for white encoder
  attachInterrupt(digitalPinToInterrupt(white_encoderPin), white_encoder_ISR, FALLING);

  /*************************
          Red motor
  **************************/
  // Configure digital pins
  pinMode(red_motorPin, OUTPUT);
  pinMode(red_encoderPin, INPUT);
  pinMode(red_encoderPin2, INPUT);
  pinMode(RedDirecPin, OUTPUT);
  pinMode(RedDirecPin, OUTPUT);

  // Configure ISR for red encoder
  attachInterrupt(digitalPinToInterrupt(red_encoderPin), red_encoder_ISR, FALLING);
}

/********************************
* loop
* 
* Main loop of code, calls compute_PID and PWM_out functions 
* All plotting on the serial monitor should go here 
* 
********************************/
void loop() {

  compute_PID_white_motor(); 
  PWM_out(output_white, WhiteDirecPin, WhiteDirecPin2, white_motorPin); 

  compute_PID_red_motor(); 
  PWM_out(output_red, RedDirecPin, RedDirecPin2, red_motorPin); 
  
}

/*************************
* PWM_out
* Inputs: PID value of desired motor, pins related to desired motor
* Outputs: None
* 
* Converts output of PID controller to direction and power for motor. Both motors use this function
* 
***************************/
void PWM_out(double pid_out, int direcPin, int direc2Pin, int motorPin) {

  // Determine direction
  if (pid_out < 0) {
    analogWrite(direcPin, 0);
    analogWrite(direc2Pin, 255);
  }
  else
  {
    analogWrite(direcPin, 255);
    analogWrite(direc2Pin, 0);
  }
  
  // Convert voltage to PWM signal
  int pwm_val = round((abs(pid_out) / SUPPLY_VOLTAGE) * 255);
  analogWrite(motorPin, pwm_val);
}

/**************************
* white_encoder_ISR
* 
* Interrupt Service Routine that triggers on every falling edge of the white motor
* Determines direction and increments or decrements displacement accordingly 
* Converts displacement into radians
* 
******************************/
void white_encoder_ISR() {

  // If the other signal is high on the falling edge of the first signal, we are going forwards
  if (digitalRead(white_encoderPin2)) {
    white_displacement++;
  }

  // Otherwise, we go backwards
  else {
    white_displacement--;
  }

  // Convert the displacement (in interrupts) to radians
  input_white = white_displacement * INTERRUPT_TO_RAD;
}


/**************************
* red_encoder_ISR
* 
* Interrupt Service Routine that triggers on every falling edge of the red motor
* Determines direction and increments or decrements displacement accordingly 
* Converts displacement into radians
* 
**************************/
void red_encoder_ISR() {

  // If the other signal is high on the falling edge of the first signal, we are going forwards
  if (digitalRead(red_encoderPin2)) {
    red_displacement++;
  }

  // Otherwise, we go backwards
  else {
    red_displacement--;
  }

  // Convert the displacement (in interrupts) to radians
  input_red = red_displacement * INTERRUPT_TO_RAD;
}


/****************************
* timer_one_ISR
* 
* Interrupt services routine that triggers every time timer 1 ticks 
* Inverts setpoint to draw a line
* 
*****************************/
void timer_one_ISR() {
  setpoint_white = -setpoint_white;
  setpoint_red = -setpoint_red;
}

/*****************************
* compute_PID_white_motor
* 
* Computes error, total error, and change in error since last reading for the white motor
* Scales error by PID constants 
* 
******************************/
void compute_PID_white_motor() {

  double error, derivativeError, errorChange; 
  int currentTime = micros(); 
  int timeChange = currentTime - white_lastTime; 

  error = setpoint_white - input_white;          // Calculate error

  if (setpoint_white != white_lastSetpoint)
    derivativeError = -input_white; 
  else
    derivativeError = error;          

  errorChange = derivativeError - white_lastError;   // Difference between error and lastError for derivative term 

  white_errorTotal += error;                      // Total error for integral term 

  double pid_val = kp_white*error + ki_white*white_errorTotal + kd_white*errorChange/timeChange;       // Calculate PID error

  output_white = constrain(pid_val, -255, 255);                                    //Constrain to useful value

  white_lastError = error; 
  white_lastTime = currentTime; 
  white_lastSetpoint = setpoint_white; 

}
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

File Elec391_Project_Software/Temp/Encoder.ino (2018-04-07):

/**************************
* laser_encoder_ISR_1
* 
* Interrupt Service Routine that triggers on every falling edge of the laser motor slot detector A
* Determines direction and increments or decrements displacement accordingly 
* Converts displacement into radians
******************************/
void laser_encoder_ISR_1() {

  // Rising Edge 
  if (digitalRead(encoderPin_laser)){
    if (digitalRead(encoderPin2_laser))
    {
      displacement_laser--;
      laser_direction = 0;
    }   
    else 
    {
      displacement_laser++;
      laser_direction = 1;
    }  
  }

  // Falling Edge
   if (!digitalRead(encoderPin_laser)){
    if (digitalRead(encoderPin2_laser))
    {
      displacement_laser++;
      laser_direction = 1;
    }  
    else 
    {
      displacement_laser--;
      laser_direction = 0;
    }  
  }

  // Convert the displacement (in interrupts) to radians
  input_laser = displacement_laser * INTERRUPT_TO_DEG;
}

/**************************
* laser_encoder_ISR_2
* 
* Interrupt Service Routine that triggers on every falling edge of the laser motor slot detector B
* Determines direction and increments or decrements displacement accordingly 
* Converts displacement into radians
******************************/
void laser_encoder_ISR_2() {

  // Rising Edge 
  if (digitalRead(encoderPin2_laser)){
    if (digitalRead(encoderPin_laser))
    {
      displacement_laser++;
      laser_direction = 1;
    }  
    else
    { 
      displacement_laser--;
      laser_direction = 0;
    } 
  }

  // Falling Edge
   if (!digitalRead(encoderPin2_laser)){
    if (digitalRead(encoderPin_laser))
    {
      displacement_laser--;
      laser_direction = 0;
    } 
    else
    { 
      displacement_laser++; 
      laser_direction = 1;
    }
  }
}

/**************************
* mirror_encoder_ISR_1
* 
* Interrupt Service Routine that triggers on every falling edge of the mirror motor slot detector A
* Determines direction and increments or decrements displacement accordingly 
* Converts displacement into radians
******************************/
void mirror_encoder_ISR_1() {

  // Rising Edge 
  if (digitalRead(encoderPin_mirror)){
    if (digitalRead(encoderPin2_mirror))
      displacement_mirror++;  
    else 
      displacement_mirror--; 
  }

  // Falling Edge
   if (!digitalRead(encoderPin_mirror)){
    if (digitalRead(encoderPin2_mirror))
      displacement_mirror--; 
    else 
      displacement_mirror++; 
  }
  input_mirror = displacement_mirror * INTERRUPT_TO_DEG;
}

/**************************
* mirror_encoder_ISR_2
* 
* Interrupt Service Routine that triggers on every falling edge of the mirror motor slot B
* Determines direction and increments or decrements displacement accordingly 
* Converts displacement into radians
******************************/
void mirror_encoder_ISR_2() {

  // Rising Edge 
  if (digitalRead(encoderPin2_mirror)){
    if (digitalRead(encoderPin_mirror))
      displacement_mirror--;  
    else 
      displacement_mirror++; 
  }

  // Falling Edge
   if (!digitalRead(encoderPin2_mirror)){
    if (digitalRead(encoderPin_mirror))
      displacement_mirror++; 
    else 
      displacement_mirror--; 
  }

  // Convert the displacement (in interrupts) to radians
  input_mirror = displacement_mirror * INTERRUPT_TO_DEG;
}

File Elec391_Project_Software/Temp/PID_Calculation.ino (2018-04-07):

void timer_one_ISR() {
  t1Flag = true; 
}

/***********************************
* Updates PID values for both motors at an interval specified by controlTime_us 
*/





void update_pid() {

//  digitalWrite(13, LOW); 
  t1Flag = false; 
  
  double kp = 0;
    
  if(laser_direction == 0)
    kp = kp_laser - LASER_MOD;
  else
    kp = kp_laser;
  
  output_laser = calculate_PID(kp, ki_laser, kd_laser, input_laser, setpoint_laser, &errorTotal_laser, &lastError_laser, &lastSetpoint_laser, &lastTime_laser);
  output_mirror = calculate_PID(kp_mirror, ki_mirror, kd_mirror, input_mirror, setpoint_mirror, &errorTotal_mirror, &lastError_mirror, &lastSetpoint_mirror, &lastTime_mirror);

  PWM_out(output_laser, motorPin_laser, LASER_DIREC_1, LASER_DIREC_2); 
  PWM_out(output_mirror, motorPin_mirror, MIRROR_DIREC_1, MIRROR_DIREC_2); 

//  digitalWrite(13, HIGH); 
}


double calculate_PID (double kp, double ki, double kd, double input, double setpoint, double *errorTotal, double *lastError, double *lastSetpoint, double *lastTime) {
  
  double error, derivativeError, errorChange, derivativeFiltered, pid_val, motor_out, currentTime, timeChange; 
  bool saturationFlag = 0;
//
  currentTime = micros()/1E6; 
  timeChange = currentTime - *lastTime; 
//  
  // P Control
  error = setpoint - input;                 // Calculate Error Term

  // I Control
  *errorTotal += error*timeChange;         // Calculate total error for integral term scaled by the change in time since last interrupt                    

  // Prevent integral windup from getting out of control. If saturationFlag is high, the I term will be ignored in the PID calculation
  if (*errorTotal > 255 || *errorTotal < -255)
    saturationFlag = 1; 
  else
    saturationFlag = 0; 
//
//  // D control
//  if (setpoint != *lastSetpoint)         // Handle derivative kick by not using the error if the setpoint changed
//    derivativeError = -input; 
//  else
  derivativeError = error;          

  errorChange = (derivativeError - *lastError)/timeChange;                // Difference between error and lastError for derivative term 

  derivativeFiltered = errorChange*FILTER_COEF/(errorChange + FILTER_COEF);         // Apply low pass filter to derivative term

  // Calculate PID values. If error term has saturated, do not use it. 
  if (saturationFlag)
    pid_val = kp*error + kd*derivativeFiltered;                                  // Do not use Ki term if we are saturating
  else
    pid_val = kp*error + ki*(*errorTotal) + kd*derivativeFiltered;       

  double output = constrain(pid_val, -SUPPLY_VOLTAGE, SUPPLY_VOLTAGE);                       // Constrain to a value within the power supply 

//  output_buffer[]
  
  *lastError = error; 
  *lastSetpoint = setpoint; 
  *lastTime = currentTime; 
  
  return output; 
}

// NOTE: WILL NEED TO TAKE ANOTHER LOOK AT LOGIC
void PWM_out(double pidVal, int motorPin, int direcPin1, int direcPin2) {
  
  // Determine direction
  if (pidVal < 0) {
    analogWrite(direcPin1, 0);        // Must write PWM signal instead of digital signal to analog pins
    analogWrite(direcPin2, 255);
  }
  else
  {
    analogWrite(direcPin1, 255);
    analogWrite(direcPin2, 0);
  }
  
  // Convert output voltage to PWM signal
  int pwmVal = round(abs(pidVal*255/SUPPLY_VOLTAGE));

  analogWrite(motorPin, pwmVal);
  
}

//void update_setpoint() {
//  setpoint_laser = setpointArray_laser[setpointIndex]; 
//  setpoint_mirror = setpointArray_mirror[setpointIndex]; 
//
////  if (setpointDir){
////    if (setpointIndex >= SETPOINT_ARRAY_SIZE-1){
////        setpointDir = false; 
////        setpointIndex--; 
////    }
////    else
////      setpointIndex++; 
////  }
////  
////  if (!setpointDir) {
////    if (setpointIndex<= 0) {
////        setpointDir= true; 
////        setpointIndex++; 
////    }
////    else 
////      setpointIndex--; 
////  }
//
////
//  if (setpointIndex >= SETPOINT_ARRAY_SIZE-1)
//    setpointIndex = 0; 
//  else
//    setpointIndex++; 
//}

void update_setpoint() {
  setpoint_laser = setpointArray_laser[setpointIndex]; 
  setpoint_mirror = setpointArray_mirror[setpointIndex]; 

//  if (setpointArray_laser[setpointIndex+1] == TERMINATION_VAL || setpointArray_mirror[setpointIndex+1] == TERMINATION_VAL) {
//    setpoint_laser = setpointArray_laser[setpointIndex]; 
//    setpoint_mirror = setpointArray_mirror[setpointIndex]; 
//    setpointDir = false; 
//  }
//
//  if (setpointIndex == 0) {
//    setpoint_laser = setpointArray_laser[setpointIndex]; 
//    setpoint_mirror = setpointArray_mirror[setpointIndex]; 
//    setpointDir = true; 
//  }
//
//  if (setpointDir) {
//    setpointIndex++; 
//  }
//  else {
//    setpointIndex--; 
//  }

  if (setpointArray_laser[setpointIndex+1]== TERMINATION_VAL)
    setpointIndex = 0; 
  else
    setpointIndex++; 
}

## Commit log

2018-02-21 Arduino Code
2018-02-21 ML&SL- Model & Encoder => SW Files
    Initial Add
    [base.SLDPRT, base.STL, base.g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]
2018-02-21 Simulink Model + Speed Tests
    [REDSpdKTests.xlsm, SpdKTests.xlsm, WHITESpdKTests.xlsm]
2018-02-21 Main PCB Altium Files
    [Current_Driver_1.SchDoc, Elec391_Project_Gen_1.PrjPcb, Top Level.SchDoc]
2018-02-22 Updated schematic, Arduino Mega model completed, no slot detector yet
    [ATMega2650.SchDoc, ArduinoMega.SchDoc, Current_Driver_1.SchDoc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]
2018-02-26 Updated version with manual traces
    [ArduinoMega.SchDoc, Current_Driver_1.SchDoc, Current_Driver_2.SchDoc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]
2018-02-26 Auto Route is like the Holocaust but worse
    [MainPCB.PcbDoc]
2018-02-27 Replaced current drivers and re-routed board, deleted old stuff
    [Current_Driver_1.SchDoc, Current_Driver_2.SchDoc, Elec391_Project_Gen_1.PrjPcb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]
2018-02-27 Cleaned up folder more, added Jake's commutator PCB
    [5 pole commutator.PcbDoc, ATMega2650.SchDoc]
2018-02-27 Organized Arduino Code into same directory
2018-03-08 Current version of PID code
2018-03-24 New PCB
    [ArduinoMega.SchDoc, Current_Driver_1.SchDoc, Current_Driver_2.SchDoc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]
2018-03-24 Current Code
2018-03-25 Fixed direction logic, kinda works with custom motor
    [Elec391_Project_Software.ino, Encoder.ino, PID_Calculation.ino]
2018-03-29 Added the interactive line drawing code. left click to add a point, spacebar to draw it, j to clear it. Map these to gui buttons instead of a keyboard event. It always draws a closed shape. next vers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
2018-04-01 Updated Arduino SW With GUI
    [circle.csv]
2018-04-03 Updated with current version of GUI (Apr 3)
2018-04-04 Crashes but otherwise works
    [LivePlot.py, LivePlotV2.py]
